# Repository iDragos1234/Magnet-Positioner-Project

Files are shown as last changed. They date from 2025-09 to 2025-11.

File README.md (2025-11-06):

# Magnet Positioner

## Introduction

Repository for the course _QIST4500 Multidisciplinary Team Project_.
In this course, our team had the task of building a gantry system used in positioning an external permanent magnet, adapted to a certain model of dilution refrigerator.
This magnet is intended for quantum control of qubits inside the refrigerator, potentially achieving this without the superconducting coil inside the refrigerator giving a static uniaxial magnetic field $B_z$ [1].
The advantage of this method is that it saves more space inside the refrigerator, allowing for more electronics and wiring to be fitted inside the refrigerator [1]. 
Another advantage is that the direction of the magnetic field $B_z$ can be changed [1]. 
In hybrid operating mode (i.e., using both the external and the internal magnet), it was experimentally shown that this could result in increased coherence times over the internal-magnet-only operating mode, while single-qubit gate fidelities stay below the fault-tolerant threshold for quantum error correction [1].

## Contents

* `magnet_positioner_cad_design/`: Folder containing all CAD files for the magnet positioning system, including a STEP file of the whole assembly.

* `magnet_xyz_positioner_code/`: Code used to control the motors. Largely unchanged from the initial code given to us.

* `magnet_data/`: Magnet measurement used for motor calibration and mapping the magnetic field. At the moment, only measurements along the x-axis are included, on a 1D grid with 1 cm spacing between neighbouring points.

* `documents/`: Relevant documents for this project, including the final report and final presentation for this project.

* `magnet_simulation.ipynb/`: Magnetic field simulations with Magpylib of the magnet used in our project.

*  `plot_magnet_data.py`: Plot of the measurements in `magnet_data/`.

## References

[1] Yu, Cecile X., et al. "Optimising germanium hole spin qubits with a room-temperature magnet." arXiv preprint arXiv:2507.03390 (2025).

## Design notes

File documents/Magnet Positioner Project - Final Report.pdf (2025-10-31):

# Magnet Positioner

Dragos, Ileana, Nian Tian Lin, Qu Tianchen and Badr Zouggari

October 31, 2025

Abstract
With the continuous scaling of semiconductor qubit architecture, the need for more space within the dilution refrigerator becomes critical, as required by the ever increasing amount of wiring and electronics inside. In this context, the superconducting magnet inside the refrigerator can become a major bottleneck, occupying valuable space inside the dilution refrigerator. Here, we present the design and development of a permanent magnet positioner outside of the the fridge to fully replace the superconducting solenoid currently being used by the Veldhorst group at QuTech. The system was modelled and manufactured considering several success criteria. To study the effect of the magnetic field at the device location, we performed simulations of the field strength around the magnet and compared them with field measurements in a single direction. Although the assembly was not completed on time, this design still shows a promising approach at addressing future scalability concerns.

## 1 Introduction

### 1.1 Theory

Semiconductor spin qubits represent one of the early studied types of qubits, providing a natural two-level system, wherein a qubit is encoded in the state of a single spin 1/2 electron/hole confined in a semiconductor quantum dot [1], [2]. The small, nanometric size (∼ 100 nm) of quantum dots provides the benefit of dense integration of many qubits on a small quantum device [2], [3]. This is an important requirement for the realization of large-scale, fault-tolerant quantum computing, as well as for relevant applications in cryptography, all of which necessitate a large number of physical qubits (more than 10⁶
) [4], [5]. Additionally, manufacturing and scaling of semiconductor devices for spin qubits is facilitated by their similarity and compatibility with classical semiconductor devices (i.e., transistors) [3], [6]. One downside is that the complexity of circuitry needed to address qubits in such quantum processors increases fast with larger number of qubits, thus limiting the maximum number of quantum dots on such devices [2], [3].

Gallium-Arsenide (GaAs) for electron spin qubit devices emerged as a first promising platform for the realization of spin qubits. GaAs provided a sparse 2D electron gas (2DEG) and allowed to isolate few (or single) electrons into a 0D space. More recently, Germanium (Ge) hole spin qubit devices have also been employed, thanks to suppressed noise from hyperfine interactions when compared to GaAs, resulting in longer coherence times [6]. The limited hyperfine interactions in Ge stem from the low abundance of nonzero nuclear spins in the environment (with the possibility of further isotopic enrichment), but also from the p-type character of the valence band [6].

An important characteristic of Ge qubits is the strong natural spin-orbit coupling which acts as a double-edged sword. On one hand, it enables all-electrical control of qubits and fast gates through electron-dipole spin resonance (EDSR). This way, shorter gate times are achieved when compared to coherence times [7]. Moreover, no other microstructures (e.g., nanomagnets) are used to control the spin, as in the case of electron spin qubits [6].

On the other hand, strong spin-charge coupling and dependence of g factors on the applied electric field imply that charge noise becomes a major nuisance for hole-spin coherence [6]. Nevertheless, it is still possible to find “sweet spots” in qubit operation such that hole-spins are not affected by charge noise. The g-tensor features strong anisotropy, meaning that the out-of-plane and in-plane components (g⊥ and g∥, respectively) differ greatly (|g⊥| ≫ |g∥|) [6]. As most Ge devices require a strong magnetic field B, even small deviations of B from the g-tensor plane can greatly affect qubit properties, resulting in different quantization axes of qubits [8].

Furthermore, the hyperfine couplings become negligible when B is in-plane, due to the Ising characteristic of hyperfine interactions [8]. Hence, limiting hyperfine interactions requires finding a second “sweet-spot” in B field alignment, but this time with respect to the hyperfine plane.

Finding an optima such that B is aligned to both of the g-tensor and hyperfine interactions¹ planes can be hard and sensitive to small angle variations of B [6], [8], and might necessitate striking a balance between the two. In this context, changing the orientation of B appears as the natural solution.

### 1.2 Problem context

The Veldhorst research group at QuTech currently operates Ge hole-spin qubit experiments by using a superconducting solenoid to generate the uniaxial magnetic field B necessary for qubit control [9]. Specifically, the solenoid is a 3-0-0 Tesla (T) magnet, meaning it can create up to 3 T on a single axis, with a bore of 200 mm (∼ 190 mm sample space) supplied by Bluefors. The uniaxial nature of B prompted the group to install an additional gantry system for moving a permanent magnet outside the dilution refrigerator [9]. This permanent magnet is used to fine-tune the magnetic field at the qubit location, thereby solving one of the limitations of the solenoid. The experiment utilized a Ge/SiGe heterostucture processor, with 10 qubits arranged in a 2D array [7]; see figure 1. Superconducting vector magnets were proposed as an alternative solution[10], but were deemed unfeasible due to higher space and heat load considerations [9].

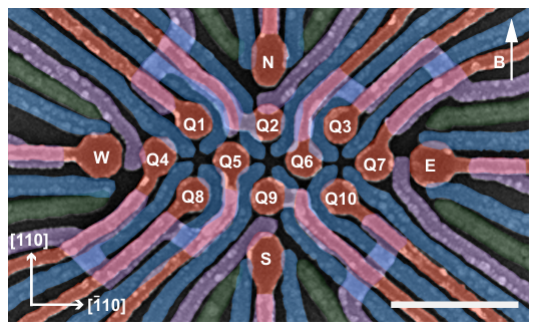
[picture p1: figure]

Figure 1: The 10 qubit physical processor (left) and its qubit layout used to test the external magnet positioner [7], [9].

While this configuration functions effectively for small-scale demonstrations with approximately 10 qubits, it presents an obstacle for the planned transition to the 1000 quantum dot project, where every bit of space inside the fridge is valuable. A successful demonstration of qubit control with the superconducting solenoid turned off and only using the permanent magnet underscores the possibility to remove the solenoid entirely [9].

A successful resolution of this challenge can have a positive impact on the scalability of semiconductor spin qubits. The dilution refrigerator’s interior represents a fixed, finite resource. However, superconducting magnets, while providing excellent field control, consume critical volume that could otherwise house cryogenic control electronics, signal conditioning components, and extensive wiring necessary for operating hundreds or thousands of qubits. Recent demonstrations have shown that room-temperature permanent magnets positioned external to the cryostat can achieve comparable qubit performance metrics, including dephasing times T

∗
2 = 13 µs and gate fidelities exceeding 99.9% [9]. This breakthrough suggests that relocating the magnetic field source outside the refrigerator is technically feasible and could unlock the spatial capacity required for qubit scale-up.

## 2 Problem statement, scope, and success criteria

### 2.1 The Core Challenge: space limitations in scaled qubit systems

Each qubit in semiconductor quantum processors uses dedicated wiring for control and readout operations. As the qubit count increases proportionally, so does the demand for coaxial lines, DC

1
It is worth noting that isotopic enrichment can remove hyperfine couplings and thus simplify this problem, to the extent that the optima for the g-tensor in-plane alignment of B dominates [8].

connections, and cryogenic electronics housed within the dilution refrigerator. The superconducting solenoid currently occupies valuable space inside the cryostat, space that must be reclaimed to accommodate the extensive circuitry required for 1000 quantum dots. Without addressing this constraint, the integration of necessary control infrastructure becomes physically impossible, effectively halting scalability efforts.

Therefore, the problem statement can be summarized as follows:

To enable scaling quantum processors from tens to thousands of qubits, an improved magnet positioning system must be designed to replace the bulky superconducting solenoid inside the dilution refrigerator, reclaiming essential space for expanded wiring and electronics.

### 2.2 Magnetic field alignment requirements

Germanium hole spin qubits exhibit strong spin-orbit interaction, which enables high-fidelity quantum gates but simultaneously creates a pronounced dependence on magnetic field orientation [9]. Precise alignment of the magnetic field to the sample plane is essential to minimize dephasing from hyperfine interactions and maximize spin control fidelity [9]. Current experiments using superconducting solenoid magnets achieve single-qubit Clifford gate fidelities above 99.9% [9]. Any alternative magnetic field solution must maintain this level of precision while simultaneously addressing the space constraints.

### 2.3 Scope of the project

In this section, the initial scope of the project is discussed. This scope was established following discussions between the team had and the project supervisor, wherein different technical challenges and initial solutions were pointed out, as outlined below. This project focuses on adapting an existing prototype magnet positioner system to the ProteoxMX dilution refrigerator in QuTech’s laboratory.

### 2.3.1 Technical challenges

- Adapting New Fridge Layout: Previously, the magnet positioner was designed for a smaller Bluefors cryogenic fridge with a different layout. In order to utilize a magnet positioner for the new ProteoxMX fridge, a new adapted frame is needed. At the same time, aiming for component reusability across the two design is desired.
- Cryogenic Temperature Effects: The Meissner effect in superconducting materials within the refrigerator can distort magnetic field distributions at different temperature stages. Understanding these temperature-dependent field modifications could be very helpful for maintaining consistent qubit operation.
- Mechanical Vibration Control: Eddy currents induced in conductive materials by moving permanent magnets can generate vibrations that propagate through the refrigerator structure. These vibrations translate to magnetic field fluctuations at the qubit location, directly degrading coherence times [11]. The project could incorporate some sort of damping mechanism to attenuate vibrations and improve overall system stability.
- Precision Positioning: Achieving 0.1 mm positioning accuracy requires careful attention to motor selection, control algorithms, and mechanical transmission systems. The implementation will explore servo-motor upgrades and gear systems between motors and leadscrews to enhance positioning precision.
- Safety Considerations: Strong permanent magnets present hazards during operation and failure scenarios. The design should include physical stops to catch the carriage in case of mechanical failure and non-magnetic rails for z-axis movement to prevent unwanted magnetic interactions.

Certain aspects lie beyond the current project scope. The design and fabrication of the qubit samples themselves, while connected to the magnet system performance, remain separate efforts. Additionally, the project focuses on the ProteoxMX [12] system; while insights may inform future adaptations to other refrigerator models, explicit multi-system compatibility is not a primary objective.

### 2.4 Success Criteria

### 2.4.1 Quantitative performance targets

- Positioning Precision: Motor control systems must achieve positioning accuracy of at least 0.1 mm in all three axes (X, Y, Z). This tolerance ensures that magnetic field variations due to positional uncertainty remain negligible compared to the qubit’s field sensitivity.
- Magnetic Field Range and Control: The system must generate magnetic fields continuously adjustable up to 25 mT at the sample location.
- Qubit Performance Preservation: The adapted magnet positioner must enable qubit dephasing times T

∗
2 at least equal to current performance with the superconducting solenoid.
- Gate Fidelity Maintenance: Single-qubit gate fidelities of ≥ 99.9% must be achieved in benchmarking tests using the external magnet system.

### 2.4.2 Functional requirements

- Magnetic Field Mapping Capability: The system must enable comprehensive characterization of the magnetic field distribution around the sample location.
- Structural Stability: The mechanical structure must exhibit sufficient rigidity to minimize vibration-induced magnetic field fluctuations.

### 2.5 Approach and implementation strategy

The project leverages a proven concept—the gantry-style permanent magnet positioner demonstrated in recent germanium qubit experiments [9]. This approach positions a room-temperature permanent magnet on a three-axis positioning system located beneath the dilution refrigerator. By maintaining the magnet external to the cryostat, the entire volume previously occupied by the superconducting solenoid becomes available for qubit sample infrastructure [9].

### 2.5.1 Advantages of the external permanent magnet approach

- Eliminates the need for bulky superconducting coils and associated infrastructure inside the cryostat, freeing space for qubit wiring and electronics [9].
- Permanent magnets require no electrical power during operation, removing a heat load source from the cryogenic environment [11].
- Comparable or superior qubit coherence times relative to superconducting solenoids, possibly due to reduced magnetic field noise [11].
- Allows in-situ adjustment of field strength and orientation without warming the refrigerator or disrupting experiments [9].

### 2.5.2 Trade-offs and limitations

- Permanent magnets generate fixed intrinsic field strengths, making continuous field adjustment more complex [9].
- Positioning mechanism introduces moving parts, creating potential vibration sources that require active damping.
- Strong permanent magnets necessitate proper shielding, mechanical stops, and careful handling.

Alternative approaches considered include hybrid systems and Halbach arrays, but the gantry-style positioning system offers the most direct path to reclaiming cryostat space while maintaining the required field control for high-fidelity qubit operations [9].

## 3 Methods and approaches

The following section will include the various steps and approaches taken to produce the magnet positioner assembly as shown in Fig. 2. The assembly is largely based on the design created by Yu et al. [9], which are improved upon to accommodate for a larger fridge and stronger magnet. The assembly was made using Autodesk Inventor, a CAD software used for 3D mechanical design and simulation. The system can be separated into a stationary part called the gantry frame and a movable part categorized as the xyz-assembly.

### 3.1 xyz movement

The movement of the magnet makes use of four NEMA 17 stepper motors with a maximum holding torque of 0.55 Nm. This choice is inspired by the way 3D printers and CNC machines operate, which enables motion on the three axes of the Cartesian coordinate system.

Using a lead screw with a 8 mm diameter and 2 mm pitch, this translates into a maximum load of ∼ 36 kg per motor, where we show the calculation in Appendix A. However, to account for the fact that the moving torque will be less than the holding torque and to allow for a margin of error, each motor should not exceed 50% of the maximum load (i.e. 18 kg per motor).

The motors are controlled with a CNC shield V3 connected to an arduino UNO board. This enables movement of three motors for all three axes with a fourth motor that can be synchronized on any axis. In this case, two motors are used to move the z direction and the remaining two move the x and y directions respectively.

To improve the positioning precision mentioned in Section 2.4.1, we have replaced the original lead screw trapezoidal nuts in the x and y directions with spring loaded anti-backlash nuts. This adds tension on the screw from both directions and prevents any unwanted motion caused by loose fitting between the two parts. A similar replacement in the z direction is not necessary, since gravity acts as a ‘natural’ anti-backlash mechanism already.

We include several SBR16 linear rails to support and guide the movement of the motors along the y and z directions. An MGN12H slider is used for the x direction.

### 3.2 Material choices

An important step in the design is to select the best materials for each part, which are influenced by several factors listed below:

- Weight: The xyz assembly in particular requires special attention due to the motors having a weight limitation as shown in Section 3.1.
- Magnetic properties: Since we work with a strong magnet, it is important to consider non-magnetic materials for safety but also to not influence the magnetic field created by the magnet.
- Rigidity: Depending on the functionality of the component, rigidity might have a higher or lower priority. Critical parts that are important for structural support require high rigidity to be able to hold up the frames above. In contrast, a stepper motor bracket can have low rigidity.

Considering the above factors, our choice of materials narrows down to three different kinds: stainless steel, PLA² filament and aluminium alloy.

While stainless steel has a high density, it offers high rigidity in return. This makes it a good option for small components that are important for stability of the entire system. For example, the z plate brackets are crucial components to connect the xyz assembly with the gantry frame. These parts are small, but have to support a lot of weight.

PLA is very lightweight with low durability and parts made from it can be easily done by a 3D printer. Any parts that hold something small in place and are not needed for the structure of the

2PLA is polylactic acid, the plastic filament used for 3D printing.

system, will be created from this material.

Aluminium alloy has a roughly three times lower density compared to stainless steel while still offering good rigidity, although not as high as stainless steel. Therefore, any large piece that will heavily impact the total weight of the assembly can be made from aluminium alloy.

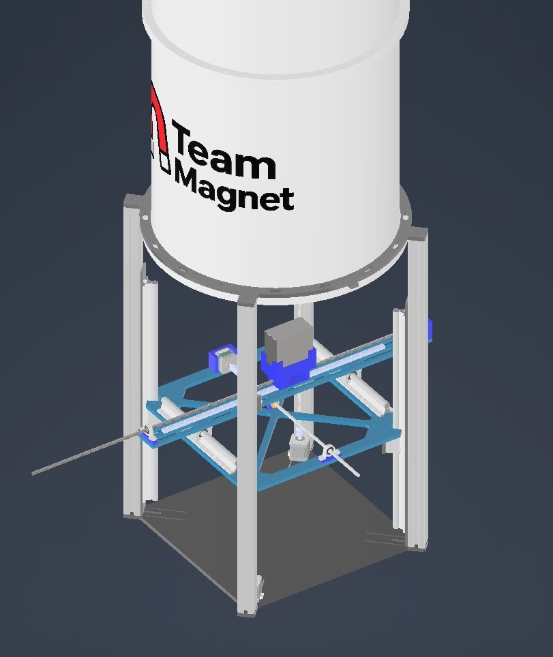
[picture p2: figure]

Figure 2: Full magnet positioner assembly attached to a cylindrical dilution refrigerator.

### 3.3 Gantry frame

Fig. 3 shows the gantry frame, which is the static outer frame of the system. The half rings and base plate are made from aluminium alloy while any brackets for vertical movement are created using stainless steel.

At the top, a ring shape is used to fit with and rest onto the rim of the dilution fridge. Compared to the smaller fridge from Ref. [9], the ProteoxMX fridge has 8 equidistant bolts protruding from the rim with 3 additional bolts appearing irregularly on halfway points between some of the regularly spaced bolts. To account for the 11 extra bolts, we have decided to create 16 holes spaced evenly (at every 22.5 degrees) around the ring. This allows for some amount of freedom to place the magnet positioner in the desired orientation. Notably, the holes themselves are designed large enough to enable up to 4 degrees of movement.

The base plate on the bottom, aside from the increased size, remains largely the same. A small modification is the addition of slotted holes in the corners of the base plate. This allows the base plate to be compatible with multiple fridge sizes, potentially future-proofing this design.

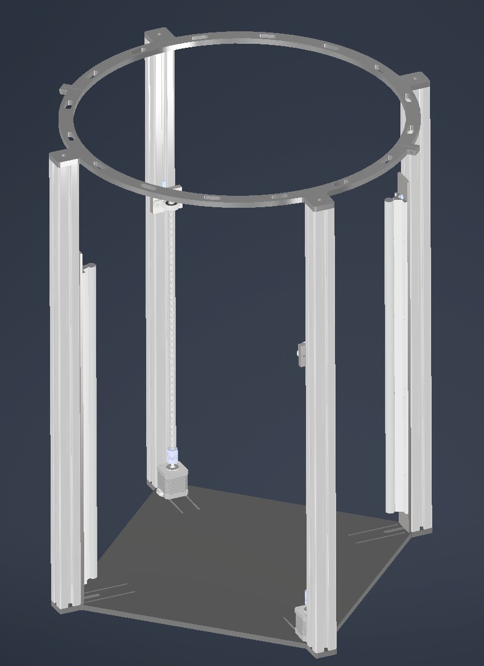
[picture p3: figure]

Figure 3: Gantry frame of the magnet positioner. The main components consist of three parts. Two half rings are created to rest on the bottom rim of the fridge, the z translation parts enable vertical movement and the base plate connects the four pillars to create a stable base.

### 3.4 xyz-assembly

Fig. 4 shows the assembly that is able to move on the z axis using the motors and rails connected to the gantry frame. Fig. 5 is mounted on top and can be moved in the y direction. Finally, the magnet itself can be moved on the guide rail in the x direction.

All of the parts indicated with dark blue and purple are not integral to the structural stability and are therefore 3D printed. The pillow block bearings and motors are mounted on top of brackets to make sure they are aligned with each other.

The plates indicated with light blue are made from aluminium alloy. The triangle shaped cutouts in Fig. 4 are added to reduce the weight of the plate without strongly impacting the structural integrity of the component. Similarly, the plate in Fig. 5 rectangular cutouts.

Before starting the manufacturing procedure of the parts, we inferred the entire weight of the xyz assembly from the CAD files. This showed that the xyz assembly totaled around 13 kg, staying well within the margin that two motors can handle in the z direction.

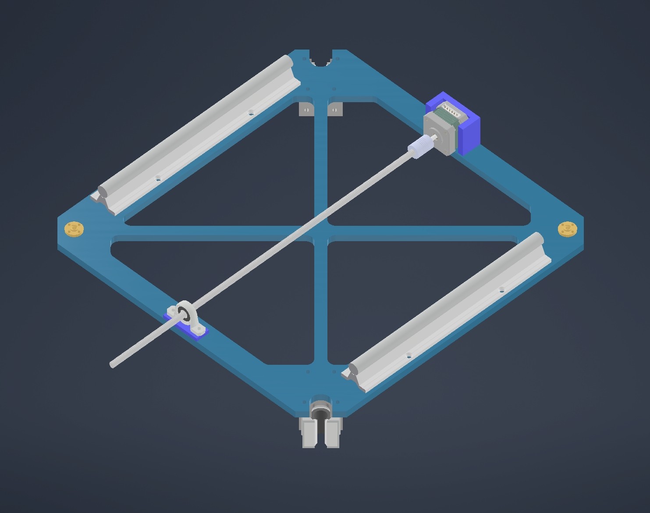
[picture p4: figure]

Figure 4: Diagram showing the movable frame of the magnet positioner in the z direction

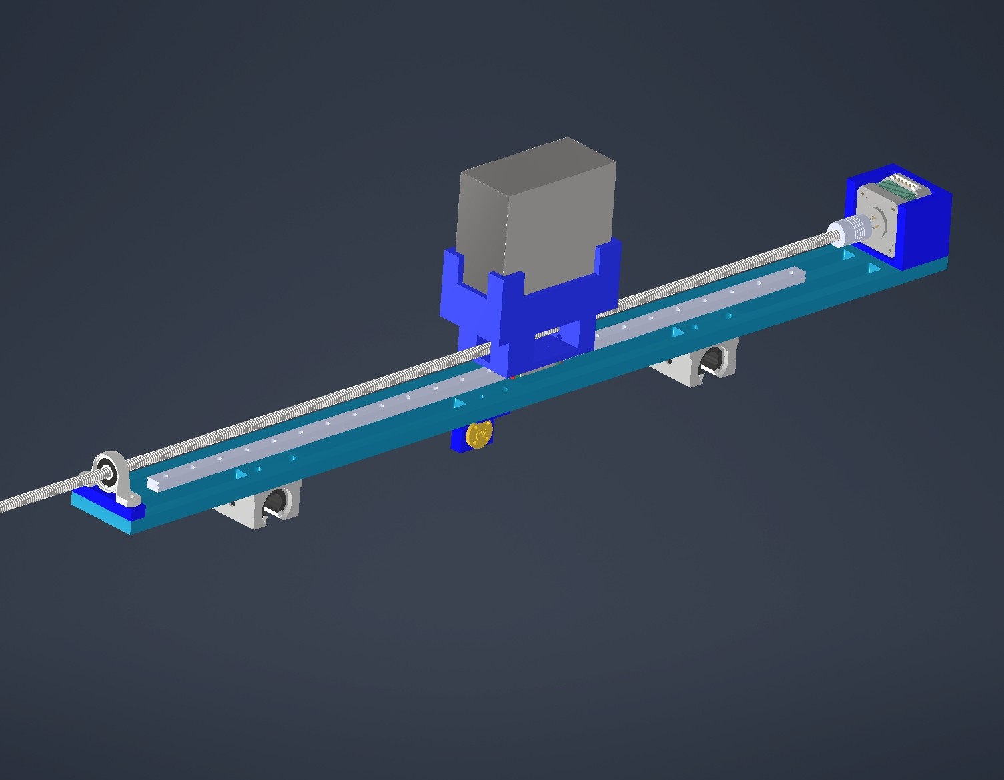
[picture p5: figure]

Figure 5: Diagram showing the movable frame of the magnet positioner in the y direction. Additionally, the magnet holder itself is movable in the x direction

## 4 Results

Our results pertain mostly to measurements of the magnetic field as its x-axis position is varied. Due to an unexpected delay in the plate fabrication, we were not able to assemble the whole magnet positioner by the time this report is written. However, we are able to theoretically analyse the magnet performance and, with the help of simulation, verify the viability of the approach.

### 4.1 Magnetic field at different distances

We measure the field strength with a 3D Hall sensor³
. The measurement setup can be seen in Fig. 6 where we move the sensor perpendicular from the centre of the magnet. We log the measurement data using evaluation software developed by Infineon Technologies that is compatible with the Hall sensor. The resulting mean field strength can be seen in Fig. 8. Here, we also compare it to the simulation using Magpylib [13][14]. This helps us verify the correctness of our simulation. The simulation is normalized by setting the magnetic field strength to be equal to the measurement result for a distance of 7cm.
The simulation of overall magnetic field in the x-y plane can be seen in Fig. 7.

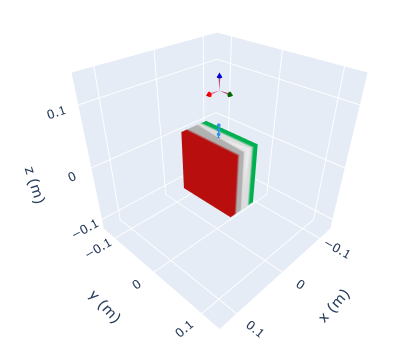
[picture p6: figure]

Figure 6: The sensor is at the centre of the magnet. Here, we move the magnet instead of the sensor. This specific instance has a 7cm distance. The red and green colour on the magnet shows its magnetisation direction and the coordinate arrows show the sensor location. The blue dotted line shows the movement for adjusting distance.

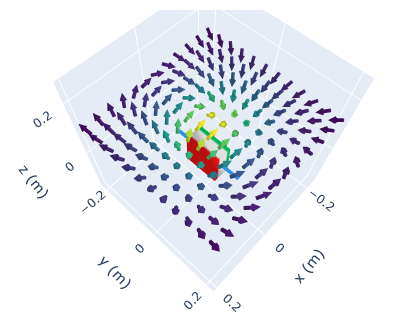
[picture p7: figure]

Figure 7: Since the magnetic field reaches the target 25mT in practice when 7cm away from the magnet surface, we show here the field distribution with z=7cm

3Model TLE493DW2B6MS2GOTOBO1 from Infineon Technologies

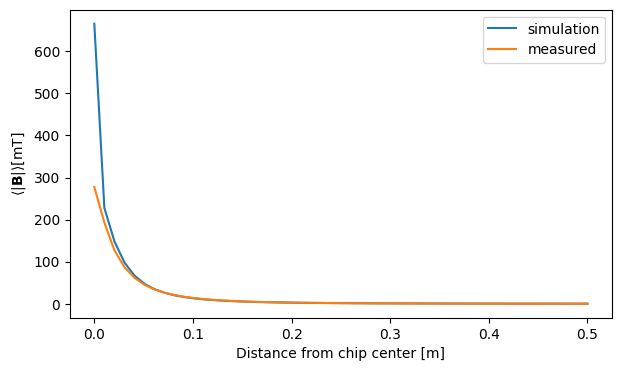
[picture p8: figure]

Figure 8: The mean field amplitude when chip is at different distances from the magnet.

### 4.2 Inhomogeneity of the magnetic field

The size of a quantum dot is at nanometer scale; therefore, although the magnetic field provided by the external permanent magnet is far from uniform, a chip with few quantum dots still experiences a close to uniform field. However, this could be a concern as one scales up the number of quantum dots on a single chip. In the Veldhorst lab, people are interested in making a 1000 quantum dot chip, with a 10∗100 square layout, where the distance between each adjacent dot is 200nm, making the quantum dots take a 20µm∗2µm area. For simplicity, we assume the chip to be a 20µm∗20µm square. This raises the question how much influence the inhomogeneity of the magnetic field will have on the future 1000 quantum dot chip.
To address this, we introduce a new quantity called deviation. For all possible magnetic field values on the chip {Bi}, the deviation d is

d = max
r,r

′
in chip

||B(r) − B(r

′
)||2

||Bchip||2

. | (1)

Which represents the maximum vector difference relative to the mean amplitude of the field across the chip.
This deviation can be estimated theoretically with the dipole moment approximation. Assuming that the magnet has a dipole moment m we can recall that the magnetic field can be approximated as:
B(r) = µ0
4π
3r(m · r)
r

5

−

m
r

3

(2)

We switch to the spherical coordinate where magnetic moment m is pointing at the positive direction of the z-axis
B(r, θ, ϕ) = µ0
4π
3|m| cos θ
r

3

rˆ −

m
r

3

(3)
Since we are already using dipole approximation, we are only interested in the first order effect of the field, which is captured by the gradient ∇B:

∂B
∂r =

−3µ0
4π
3|m| cos θ
r

4

rˆ −

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
∂θ = −

µ0
4π

3|m|sin θ
r

3

rˆ | (6)

∂B
∂ϕ = 0 | (7)

The deviation can be first-order approximated as

d = max
a∈{0}×[0,a]×[0,a]

||a · ∇B||2
||B||2

(8)

where a is some relative position within the chip with width a.
Since we want in-plane magnetic field, the chip position will be perpendicular to the moment m · r = 0 or θ =

π
2

and thus the first term in dipole magnetic field expression vanish, thus

∂B

∂θ m·r=0

= −3||B||2r. ˆ | (9)

Thus if we express the gradient in normalized ˆr, ˆθ, ϕˆ basis

∇B
||B||2
θ= π
2

=

3
r

ˆθ −
3
r

rˆ 0

(10)

We see that the deviation will have the same 3
r

decay in the ˆr or ˆθ direction, but it will vanish in the ϕˆ direction. Since our chip is in ˆθ − ϕˆ plane, the deviation is

d =

3a
r

(11)

Deviation with other chip orientations can also be derived from (10).
In order to cross-check whether the dipole approximation fits our case, we also perform a simulation. Here, we assume that permeability is constant and the magnet has uniform magnetisation. To evaluate the magnetic field gradient, we use the same setup as the previous subsection as seen in Fig. 6.
We collect samples {Bi} of the magnetic field from 400 evenly spaced locations in the 20µm × 20µm chip and the deviation estimator becomes:

d = max
i,j

||Bi − Bj ||2
⟨||B||2⟩

Note that deviation as a relative quantity is independent of the magnetisation strength of the actual magnet.

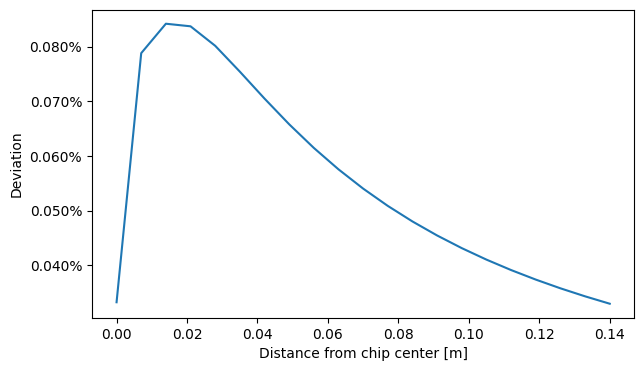
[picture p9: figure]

Figure 9: The deviation when chip is at different distances from the magnet.

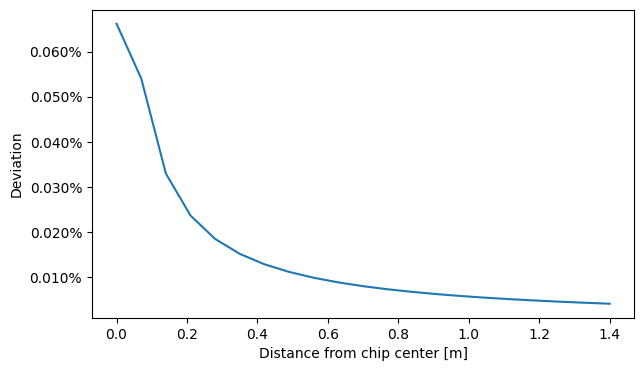
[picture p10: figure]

Figure 10: We see full dipole approximation regime for z > 0.2m.

From the simulation results in Fig. 9,10, we can see that the magnetic deviation is more than three orders of magnitude lower than the mean magnetic field. Since in fabrication it is common to have the g-factor vary by a factor of 2 across different quantum dots [15], the magnetic field gradient will not be the dominating term for qubit frequency fluctuations.

We also see that deviation decreases as expected from our theoretical report except when the distance is very close. This is expected since the dipole approximation breaks down in close range. Instead, we see a sharp increase from zero. Low deviation for a close chip is largely due to the magnetic field being almost uniform near its surface. Thus we have a peak deviation between uniform approximation regime and dipolar approximation regime.

We may also be interested in how the deviation depends, on the orientation of the chip. We choose the distance to be 7cm where the field is around 25mT. Here, we also see how the simulation fits accurately with the theoretical prediction.

When rotating along the ˆθ direction in Fig. 11, we see two peak deviations at π/2 and 3π/2. with peak value being √
2 times higher than the minimum value. Since the chip is in ˆr − ˆθ plane, the deviation has contribution from both directions

d = ||³a
r

ˆθ −

3a
r

rˆ||2 =

3

√
2a
r

(12)

When rotating along the ϕˆ direction in Fig. 12, since contributions are the same from ˆr and ˆθ, we see no deviation difference up to first order.
When rotating along the ˆr direction in Fig. 13, the chip remain in ˆθ−ϕˆ plane. However rotating the square chip changes the maximum distance of the ˆθ direction as it vary from side length to diagonal length. Thus we see 4 peaks at π/4, 3π/4, 5π/4, 7π/4 with the peak √
2 times bigger than
the minimum deviation.
Therefore, different orientations of the chip will result in at most a factor of √ 2 difference for
the deviation.

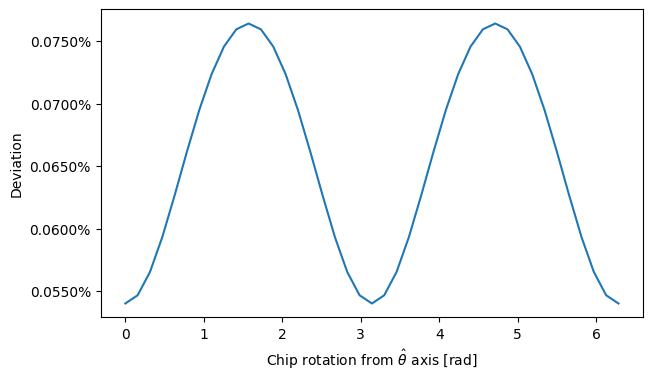
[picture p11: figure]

Figure 11: The deviation when chip is at different distances from the magnet.

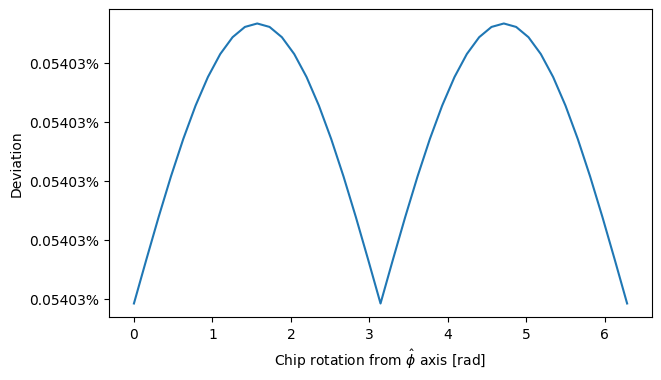
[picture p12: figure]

Figure 12: The deviation when chip is at different distances from the magnet.

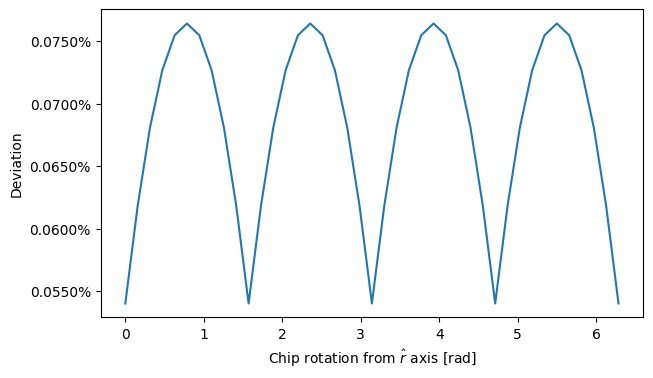
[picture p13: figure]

Figure 13: The deviation when chip is at different distances from the magnet.

### 4.3 Noise analysis

The next thing we want to estimate is the potential noise an external magnet can bring to the qubit. In previous work [9], the hysteresis effect is observed from the motor for magnet movement. This leads to approximately 50µm offset per start-and stop event for the movement of 1mm. However, this should not be considered as decohering noise since such an offset can be predicted/compensated. Also, such an offset only exists when we want to reposition the magnet and can be accurately measured when the magnet is still. The main noise comes from potential random vibration of the positioner, which is more prone to these disturbances since the magnet is no longer inside the concealed fridge.

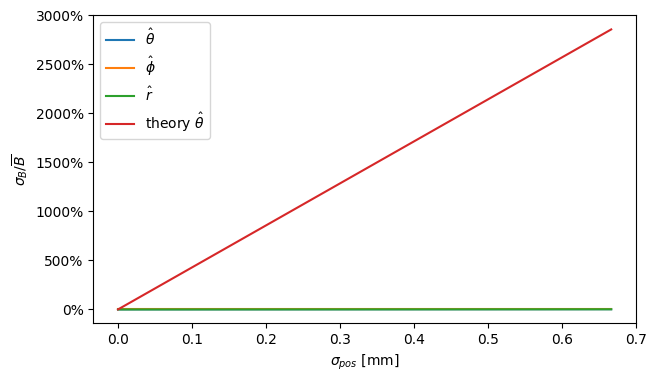
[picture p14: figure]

Figure 14: The deviation when chip is at different distances from the magnet. We also show the theoretical prediction of the dependency for ˆθ direction, which is in line with simulation result.

The Larmor frequency of quantum dot qubits usually ranges from a few hundred MHz to a few GHz. In comparison, the mechanical vibration of the positioner has a far lower frequency. Thus, we can model noise from the magnet as a quasistatic noise. Assuming that the offset amplitude of

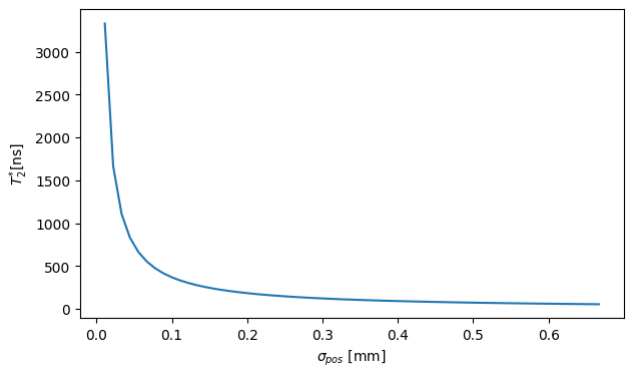
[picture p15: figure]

Figure 15: How T

∗
2 depend on the standard deviation of the magnet position.

the magnet follows a gaussian distribution that does not exceed 2mm, aka 3σpos < 2mm. Since the fluctuations are small, the resulting magnetic deviation also follows a gaussian distribution, and the relation can be calculated using (10) in the same way we calculated the deviation in the previous section. From Fig. 14, we see that only vibration from the ˆr, ˆθ direction will cause magnetic field fluctuation. At the same time, only ˆr direction vibration will have a magnetic field deviation in ˆθ direction – parallel to the magnetic field, which has a first order effect on the magnetic field amplitude. Since the larmor frequency is proportional to the field amplitude, the resulting Larmor frequency distribution becomes

P(ω) = 1
√
2πσω

e

−

(ω−ωL)

2

2σ2
| ω | (13)

σω = ωL

σB
B
= ωL | 3σpos,r
r
| | (14)

For quasistatic noise, the coherence function is the Fourier transform of the noise distribution from which we can deduce T

∗
2

time:

f(t) = ⟨S

+(t)⟩ = ⟨S

+

Z +∞

−∞

P(ω)e

itωdω⟩ | (15)

= ⟨S

+e

iωLt
e

−σ2
ωt

2
2 | ⟩ | (16)

= f(0)e

iωLt
e

−σ2
ωt

2
2 | | (17)

= f(0)e

iωLt
e

− ¹
2
| t T ∗
| 2

2
, T ∗
2 =

1
σω
| | (18)

We will thus have a gaussian decay for the qubit coherence with relaxation time T

∗
2
| | inverse
to σω. From Fig. 15, we can see the estimation of T

∗
2

time assuming the larmor frequency to be 1GHz. We can see that for strong vibration, the T

∗
2

is considerably affected. Although we can argue that such quasistatic noise can be largely cancelled by dynamical decoupling, we still see that such a positioner could be sensitive to mechanical vibration in certain cases.

In conclusion, the T

∗
2

is sensitive to vibration on the ˆr direction and could affect the qubit performance when strong vibration exists. Given the setup in our positioner, this corresponds to vertical vibration of the magnet.

### 4.4 Data management

All CAD designs for the complete setup, along with the specific parts discussed in Chapter 3, and the simulation data outlined in this chapter with the associated code, are available in our GitHub repository [16].

## 5 Discussion

### 5.1 Reflection

The development of the magnet positioning system was not fully completed due to delays in the delivery of several critical manufactured components. These parts, mainly the X-plate and Z-plate which were essential for the mechanical assembly and calibration of the positioning mechanism, did not arrive in time to allow for integration and testing during the project period. As a result, key functionalities such as positional feedback verification and dynamic control tuning could not be carried out as planned.

The delay was mainly due to our reliance on external manufacturing and the lack of sufficient buffer time in the project schedule to account for possible production or shipping setbacks. Additionally, some design iterations were finalized later than expected, which further compressed the available window for ordering and assembly.

In retrospect, this issue could have been mitigated through earlier procurement planning and risk management. Placing the manufacturing orders sooner, or designing provisional substitute components for early-stage testing could have reduced dependency on external timelines. Improved communication with the manufacturer to track progress and confirm lead times would also have helped anticipate and respond to potential delays.

### 5.2 Success criteria evaluation

Even though we were not able to finalize the product, we were still able to achieve some intermediate progress. This progress will be assessed by evaluating our success criteria.
The project began with a set of predefined success criteria that guided the design and development of the magnet positioning system. In this section, we reflect on how these criteria were addressed and evaluate the corresponding outcomes.
- Positioning Precision: The motor control system was required to achieve a positioning accuracy of at least 0.1 mm in all three spatial axes to ensure magnetic field stability relative to the qubit’s field sensitivity. Due to the incomplete assembly of the mechanical structure, this specification could only be experimentally verified in the x direction with the anti backlash nut. However, the same principle should apply for the y direction.
- Magnetic Field Range and Control: The system was designed to provide continuously adjustable magnetic fields up to 25 mT at the sample location. Based on measurements compared to simulation results and magnetic field calculations (described in section 4.1), we are confident that the current electromagnet configuration fulfills this requirement. The range of the magnet positioner in the Z-direction was designed with these specific requirements in mind.
- Qubit Performance Preservation: A key criterion was ensuring that the new magnet positioner maintains qubit dephasing times (T

∗
2

) comparable to those obtained using the existing superconducting solenoid. Since the physical assembly was not completed, this verification could not be performed. This assessment will ultimately depend on future testing conducted by the research group that integrates the system with their qubit setup. Instead, we estimated the T

∗
2

for the qubit with reasonable assumptions and simulation. It shows the T

∗
2

is sensitive to the vibration strength and it is only sensitive to vibrations perpendicular to the magnet. In our framework, this correspond to vertical vibration.

- Gate Fidelity Maintenance: Achieving single-qubit gate fidelities of at least 99.9% in benchmarking tests requires integration of the magnet system with the quantum hardware. As testing was contingent upon a completed setup, this requirement remains to be verified in collaboration with the end users during the next stage of project deployment.

- Magnetic Field Mapping Capability: Making use of a Hall sensor with associated evaluation software, we showed the capability to log and save the magnetic field measurements in a single direction. Furthermore, after some postprocessing we were able to visualize the field strength and compare it to our simulations which can be seen in Fig. 6. Hence, we believe that the full mapping of the magnetic field is also possible once the entire assembly is completed.
- Structural Stability: The structural design aims to minimize vibration-induced field fluctuations through high rigidity and reduced mechanical resonance. Although the final structure has not yet been assembled, material choices and design simulations indicate that the mechanical stability criterion is likely to be met once manufacturing and integration are completed.

In summary, the success criteria related to positioning precision, magnetic field range and mapping capability were partially achieved within the scope of the project. Criteria dependent on the physical assembly and integration, such as positioning precision, qubit performance preservation, gate fidelity maintenance, and structural stability, remain to be validated. Overall, the design phase established a strong foundation to meet all goals once the remaining components are delivered and assembled.

### 5.3 Future Plan of Attack

This section outlines a proposed plan for achieving and validating the success criteria that were not fully met during the initial project phase. Each subsection focuses on a specific criterium, detailing methods of assessment, potential challenges, and further steps to ensure successful realization.

### 5.3.1 Positioning Precision

To verify the required positioning accuracy of better than 0.1 mm in all three axes, precision calibration experiments will be conducted once the mechanical structure is assembled. The plan could include integrating high-resolution optical encoders or laser displacement sensors onto each axis to measure actual movement relative to commanded positions.

Evaluation will involve repeated motion sequences and comparison between commanded and measured displacements to determine both static and dynamic precision. If deviations exceed the tolerance, potential improvements include refining motor control parameters, improving the mounting rigidity, or looking into higher quality motors.

### 5.3.2 Qubit Performance Preservation

To assess the influence of the magnet positioner on qubit dephasing times (T

∗
2

), the system will be
tested in conjunction with a qubit setup operated by the partner research group. The procedure involves performing Ramsey or spin echo experiments under various magnetic field configurations generated by the positioner. The resulting T

∗
2 values will be compared to baseline results obtained with the superconducting solenoid.

Should the T

∗
2

times degrade noticeably, the next step will be to identify possible noise sources introduced by the new system, such as current fluctuations, magnetic field instabilities, or mechanical vibrations. Adjusting current stabilization, improving shielding, or refining control electronics could be considered to mitigate these effects.

### 5.3.3 Gate Fidelity Maintenance

The goal of maintaining gate fidelities above 99.9% can be tested using randomized benchmarking experiments with the magnet positioner integrated into the quantum hardware setup. This approach quantifies the average error per gate under varying magnetic field conditions.

If the measured fidelities fall below the target value, diagnostic tests should be performed to identify whether the issue stems from magnetic field noise, cross-talk between control channels, or thermal effects induced by the magnet coils. Based on these findings, the control algorithms and magnetic stabilization methods can be optimized, or additional passive and active noise suppression techniques can be introduced.

### 5.3.4 Structural Stability

After assembly, the structural stability will be experimentally validated by measuring vibration spectra of the positioning system during operation. This can be achieved using accelerometers or laser vibrometers attached to key structural components. The amplitude and frequency of mechanical oscillations will be compared to the frequencies relevant to qubit sensitivity.

If significant vibration modes are detected near critical operating frequencies, reinforcement of the frame or damping materials can be introduced to shift resonances away from sensitive bands. Additionally, mechanical coupling between moving parts can be optimized to further minimize unwanted vibrations.

## 6 Interdisciplinarity and teamwork

In this section, the various scientific disciplines explored in this project are discussed, as well as the teamwork during the project.

### 6.1 Interdisciplinary aspects

The interdisciplinary aspects of the Magnet Positioner project are central to both the process and the solution, drawing on expertise and methodologies from physics, engineering, computer science, and system design.

The project leverages methods and knowledge from quantum physics to define the requirements for magnetic field alignment and qubit performance, as well as to interpret simulation results relating to magnetic noise and field homogeneity. Engineering design principles guide the development of hardware structures, including the selection of materials for rigidity, weight, and magnetic properties, and the mechanical design of the gantry frame and xyz-movement assembly. Computer science and automation are incorporated through the use of CAD modeling (Autodesk Inventor) for 3D simulation, control algorithms for the stepper motors (Arduino UNO interface), and data analysis software for magnetic field mapping and real-time monitoring.

The process brings together simulation-based analysis, mechanical design, electronic control, and risk management strategies. The solution’s success criteria span quantitative (positioning accuracy, field range, gate fidelity) and qualitative (mechanical stability, safety protocols) metrics, requiring cross-disciplinary knowledge and skills.

### 6.2 Collaboration and team dynamics

At the start of the project, each member of the team already had some idea where there interests would lie within this project. As explained in the section above, the project consisted of various disciplines, where each member of the team felt slightly more comfortable to some disciplines than others. Given the various engineering aspects to this projects, each member of the team could start the project with a certain focus (e.g. figuring out the motors or starting with the CAD design). We would meet up often to show each other what we worked on, which made the start of the project very smooth. Moreover, all the team members were interested in all the aspects of the project, which meant that the team would have numerous useful discussions about what the next steps would be. This way of working persisted throughout the duration of the project and all team members are content with the way it went.

However, the project was not finished in time, which begs the question of how this came to be. The team suspects that this could have been avoided if the team was more conscious of the manufacturing times of the parts. Many critical parts are still not finished, which was the main reason this project could not be finished in time. Some delays were out of the control of the team, however this situation could have been avoided if the urgency had existed right at the start of the project. In hindsight, the team should have treated the manufacturing team with more urgency. Moreover, dummy parts could have been designed and manufactured to at least provide some clarity on some of the success criteria.

All in all, the team does feel that a lot has been accomplished during the duration of the project. This includes: a complete CAD design of the magnet positioner, motor testing with some of the bigger and heavier parts, magnetic field simulations and software to map the magnetic field with a comparison to real measurements, albeit only in one direction. Even though the project was not completed as we envisioned it to be at the start, the team is confident that a future project team can build upon our results and finish the project as it was intended to be.

## 7 Acknowledgments

During this project, we have had the absolute pleasure of working together with our team supervisor, Sasha Ivlev. He has been an enormous help during the process by answering our questions, providing new ideas and feedback, and providing guidance during the entire process. The team would like to thank him for the opportunity to work together on this project and hope that our work will be useful to him and the entire research group. Additionally, the team would like to thank the manufacturing team, specifically Nico Alberts, by providing us with guidance during the design process and the fabrication of tailor-made builds.

The team would also like to acknowledge that the usage of AI was limited during the entirety of the project, with some exceptions to help with literature review and understanding theoretical concepts better.

## References

[1] D. Loss and D. P. DiVincenzo, “Quantum computation with quantum dots,” Physical Review A, vol. 57, no. 1, pp. 120–126, Jan. 1998, issn: 1094-1622. doi: 10.1103/physreva.57.120. (https://doi.org/10.1103/physreva.57.120) [Online]. Available: http://dx.doi.org/10.1103/PhysRevA.57.120.
[2] G. Burkard, T. D. Ladd, A. Pan, J. M. Nichol, and J. R. Petta, “Semiconductor spin qubits,” Rev. Mod. Phys., vol. 95, p. 025 003, 2 Jun. 2023. doi: 10.1103/RevModPhys.95.025003. (https://doi.org/10.1103/RevModPhys.95.025003) [Online]. Available: https://link.aps.org/doi/10.1103/RevModPhys.95.025003.
[3] L. M. K. Vandersypen et al., “Interfacing spin qubits in quantum dots and donors—hot, dense, and coherent,” npj Quantum Information, vol. 3, no. 1, Sep. 2017, issn: 2056-6387. doi: 10.1038/s41534-017-0038-y. (https://doi.org/10.1038/s41534-017-0038-y) [Online]. Available: http://dx.doi.org/10.1038/s41534-017-0038-y. (http://dx.doi.org/10.1038/s41534-017-0038-y)
[4] A. G. Fowler, M. Mariantoni, J. M. Martinis, and A. N. Cleland, “Surface codes: Towards practical large-scale quantum computation,” Physical Review A, vol. 86, no. 3, Sep. 2012, issn: 1094-1622. doi: 10.1103/physreva.86.032324. (https://doi.org/10.1103/physreva.86.032324) [Online]. Available: http://dx.doi.org/10.1103/PhysRevA.86.032324. (http://dx.doi.org/10.1103/PhysRevA.86.032324)
[5] C. Gidney, “How to factor 2048 bit rsa integers with less than a million noisy qubits,” 2025. arXiv: 2505.15917 [quant-ph]. [Online]. Available: https://arxiv.org/abs/2505.15917.
[6] G. Scappucci et al., “The germanium quantum information route,” Nature Reviews Materials, vol. 6, no. 10, pp. 926–943, Dec. 2020, issn: 2058-8437. doi: 10.1038/s41578-020-00262-z. (https://doi.org/10.1038/s41578-020-00262-z) [Online]. Available: http://dx.doi.org/10.1038/s41578-020-00262-z.
[7] V. John et al., “A two-dimensional 10-qubit array in germanium with robust and localised qubit control,” 2025. arXiv: 2412.16044 [cond-mat.mes-hall]. (https://arxiv.org/abs/2412.16044) [Online]. Available: https: //arxiv.org/abs/2412.16044.
[8] N. W. Hendrickx et al., “Sweet-spot operation of a germanium hole spin qubit with highly anisotropic noise sensitivity,” Nature Materials, vol. 23, no. 7, pp. 920–927, May 2024, issn: 1476-4660. doi: 10.1038/s41563-024-01857-5. (https://doi.org/10.1038/s41563-024-01857-5) [Online]. Available: http://dx.doi.org/10.1038/s41563-024-01857-5. (http://dx.doi.org/10.1038/s41563-024-01857-5)
[9] C. X. Yu et al., “Optimising germanium hole spin qubits with a room-temperature magnet,” 2025. arXiv: 2507.03390 [quant-ph]. (https://arxiv.org/abs/2507.03390) [Online]. Available: https://arxiv.org/abs/2507. 03390. (https://arxiv.org/abs/2507.03390)
[10] G. Da Prato, Y. Yu, R. Bode, and S. Gr¨oblacher, “Step-by-step design guide of a cryogenic three-axis vector magnet,” Review of Scientific Instruments, vol. 96, no. 6, Jun. 2025, issn: 1089-7623. doi: 10.1063/5.0270187. (https://doi.org/10.1063/5.0270187) [Online]. Available: http://dx.doi.org/10.1063/5. 0270187. (http://dx.doi.org/10.1063/5.0270187)
[11] C. Adambukulam et al., “An ultra-stable 1.5 T permanent magnet assembly for qubit experiments at cryogenic temperatures,” Review of Scientific Instruments, vol. 92, no. 8, 2021.

[12] Proteox MX dilution refrigerator, https://nanoscience.oxinst.com/products/proteoxmx, Accessed: 31-10-2025.
[13] M. Ortner and L. G. C. Bandeira, “Magpylib: A free python package for magnetic field computation,” SoftwareX, vol. 11, p. 100 466, 2020.
[14] Michael-Ortner et al., Magpylib, version 5.2.1, Jun. 25, 2023. [Online]. Available: https : //magpylib.readthedocs.io/en/latest/.
[15] C.-A. Wang et al., “Operating semiconductor quantum processors with hopping spins,” Science, vol. 385, no. 6707, pp. 447–452, 2024. doi: 10.1126/science.ado5915. (https://doi.org/10.1126/science.ado5915) eprint: https: //www.science.org/doi/pdf/10.1126/science.ado5915. [Online]. Available: https: //www.science.org/doi/abs/10.1126/science.ado5915.
[16] Magnet-positioner-project, https : / / github . com / iDragos1234 / Magnet - Positioner -Project, (https://github.com/iDragos1234/Magnet-Positioner-Project) GitHub repository., 2025.

## A Maximum weight calculation of NEMA 17 stepper motors

Given that a single stepper motor has a maximum holding torque of τ = 0.55 Nm and a lead screw radius of r = 4 mm, it easily follows from the torque formula

τ = r × FE,

that the effort force is FE = 137.5 N. The efficiency of the lead screw is given by

η =

tan(α)
tan(α + β)

,

where α is the lead angle and β is the friction angle. Given that the lead screw has a pitch P = 2 mm and assuming the coefficient of friction between the rotating components is f = 0.3, we find α = tan⁻¹
(

P
2πr

) ≈ 4.550◦ and β = tan⁻¹

(f) ≈ 16.699◦
. Therefore the lead screw has an efficiency of η ≈ 20.4%.
Using this and the velocity ratio of the lead screw V R = 2πr/P = 4π, it follows that the mechanical advantage is MA = V R · η ≈ 2.57. Finally, the load force is given by

FL = FE · MA

resulting in FL = 353.6 N, or equivalently a weight of around 36 kg per motor.

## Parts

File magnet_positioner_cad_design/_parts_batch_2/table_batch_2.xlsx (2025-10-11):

Item number | Item | Part file (.stp) | Drawing file (.pdf) | Quantity | Material | Other specifications
#1 | Z-plate | z_plate.stp | z_plate.pdf | x1 | Aluminium alloy | Apply deburring on sharp edges and corners as needed
#2 | X-plate | x_plate.stp | x_plate.pdf | x1 | Aluminium alloy | Apply deburring on sharp edges and corners as needed

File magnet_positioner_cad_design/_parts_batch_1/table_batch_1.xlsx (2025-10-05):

Item number | Item | Part file (.stp) | Drawing file (.pdf) | Quantity | Material | Other specifications
#1 | Half ring | half_ring.stp | half_ring.pdf | x2 | Aluminium alloy | Apply deburring on sharp edges and corners as needed
#2 | Base plate | base_plate.stp | base_plate.pdf | x1 | Aluminium alloy | Apply deburring on sharp edges and corners as needed
#3 | Z-rail bracket | z_rail_bracket.stp | z_rail_bracket.pdf | x2 | Stainless steel | Apply deburring on sharp edges and corners as needed
#4 | Z-translator bracket | z_translator_bracket.stp | z_translator_bracket.pdf | x2 | Stainless steel | Apply deburring on sharp edges and corners as needed
#5 | Z-plate bracket | z_plate_bracket.stp | z_plate_bracket.pdf | x2 | Stainless steel | Apply deburring on sharp edges and corners as needed
#6 | Profile bars | profile_bar.stp | N/A | x4 | Aluminium alloy | Size 40x40. Length 850 mm. Threading for M8 screws

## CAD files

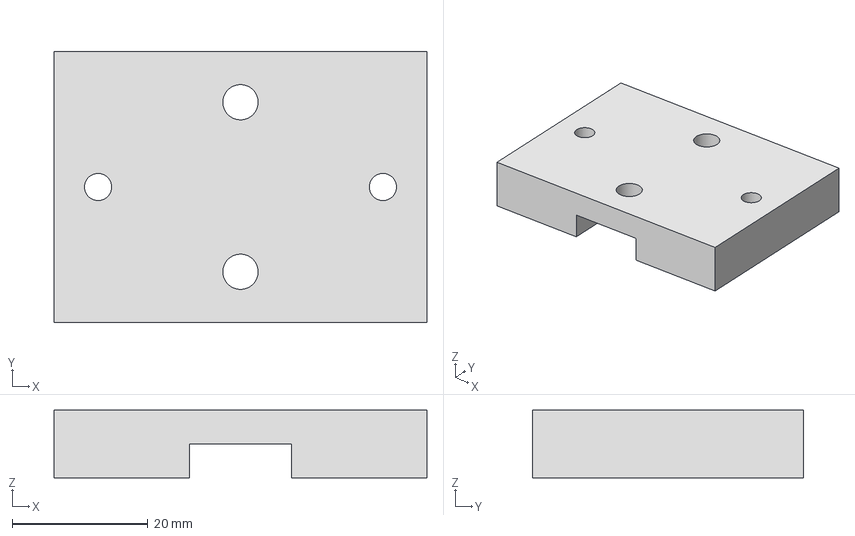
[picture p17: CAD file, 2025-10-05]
magnet_positioner_cad_design/_parts_batch_1/z_translator_bracket.stp
55.0 x 40.0 x 10.0 mm

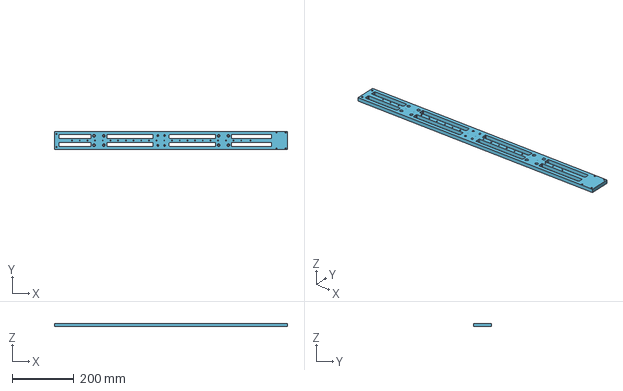
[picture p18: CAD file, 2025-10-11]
magnet_positioner_cad_design/_parts_batch_2/x_plate.stp
757.5 x 60.0 x 10.0 mm

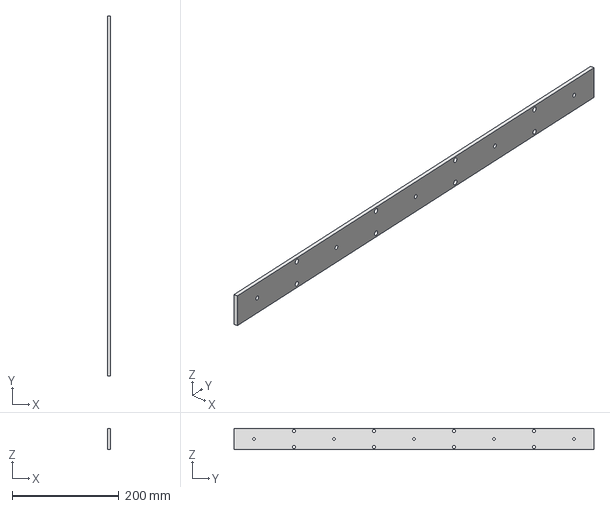
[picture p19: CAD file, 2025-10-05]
magnet_positioner_cad_design/_parts_batch_1/z_rail_bracket.stp
5.00 x 675.0 x 40.0 mm

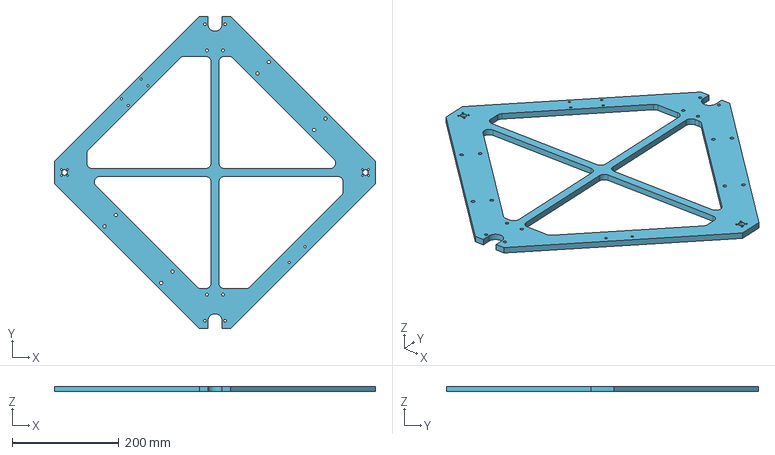
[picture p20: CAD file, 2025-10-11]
magnet_positioner_cad_design/_parts_batch_2/z_plate.stp
601.0 x 585.0 x 10.0 mm

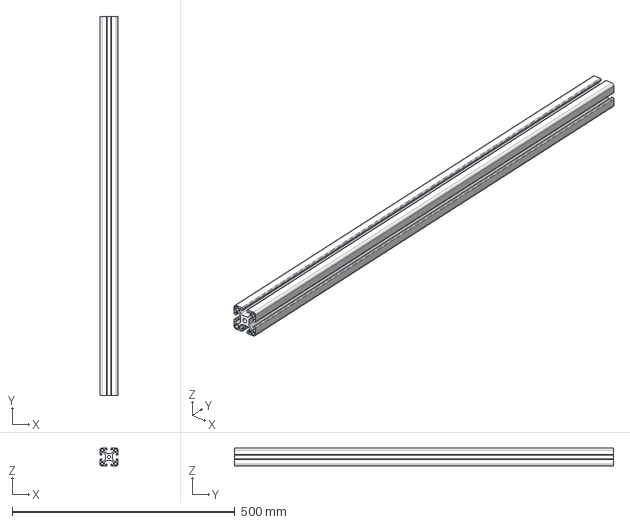
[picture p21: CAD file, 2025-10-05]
magnet_positioner_cad_design/_parts_batch_1/profile_bar.stp
40.0 x 850.0 x 40.0 mm

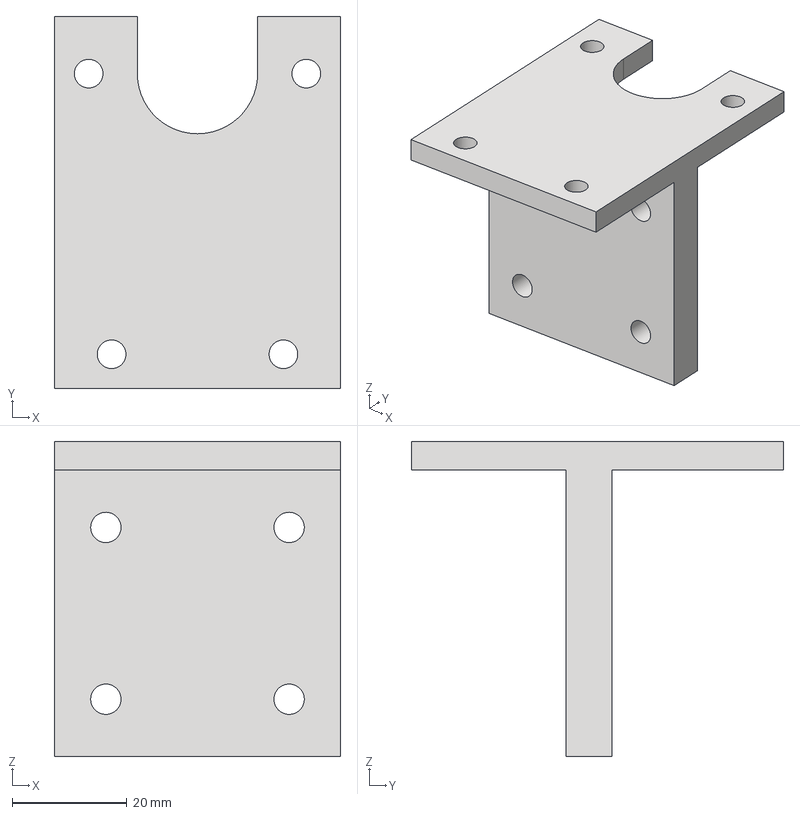
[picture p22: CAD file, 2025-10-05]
magnet_positioner_cad_design/_parts_batch_1/z_plate_bracket.stp
50.0 x 65.0 x 55.0 mm

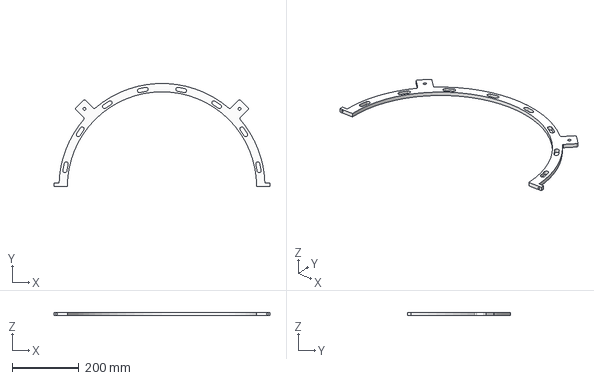
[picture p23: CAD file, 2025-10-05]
magnet_positioner_cad_design/_parts_batch_1/half_ring.stp
645.0 x 307.2 x 10.0 mm

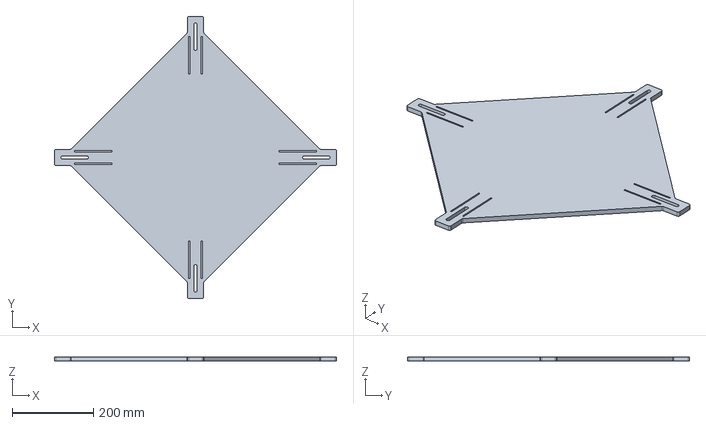
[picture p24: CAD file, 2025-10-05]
magnet_positioner_cad_design/_parts_batch_1/base_plate.stp
695.0 x 695.0 x 10.0 mm

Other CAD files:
magnet_positioner_cad_design/drawings/z_plate.dwg
magnet_positioner_cad_design/drawings/x_plate.dwg
magnet_positioner_cad_design/gantry_frame/half_ring.dwg
magnet_positioner_cad_design/drawings/half_ring.dwg
magnet_positioner_cad_design/gantry_frame/Rail_bracket.dwg
magnet_positioner_cad_design/gantry_frame/base_plate.dwg
magnet_positioner_cad_design/drawings/Rail_bracket.dwg
magnet_positioner_cad_design/drawings/base_plate.dwg
magnet_positioner_cad_design/gantry_frame/Leadscrew Bearing Bracket.dwg
magnet_positioner_cad_design/drawings/Leadscrew Bearing Bracket.dwg
magnet_positioner_cad_design/gantry_frame/base_plate.ipt
magnet_positioner_cad_design/gantry_frame/full_ring.iam
magnet_positioner_cad_design/gantry_frame/gantry_frame.iam
magnet_positioner_cad_design/gantry_frame/half_ring.ipt
magnet_positioner_cad_design/gantry_frame/square_bar.ipt
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

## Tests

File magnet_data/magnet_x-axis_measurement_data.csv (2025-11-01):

 | Magnet-sensor distance [cm] | Bx[mT] | By[mT] | Bz[mT] | Bx[LSB] | By[LSB] | Bz[LSB] | Temperature[C] | Mode[MCM=0,ULOW_POWER=1,LOW_POWER=2,FAST=3]
0 | 0 | -54.95 | -277.63 | 24.95 | -1621 | -8190 | 736 | 20.26 | 2
1 | 0 | -55.05 | -277.63 | 24.95 | -1624 | -8190 | 736 | 20.33 | 2
2 | 0 | -54.92 | -277.63 | 24.92 | -1620 | -8190 | 735 | 20.39 | 2
3 | 0 | -54.88 | -277.63 | 24.88 | -1619 | -8190 | 734 | 20.39 | 2
4 | 0 | -55.08 | -277.63 | 24.92 | -1625 | -8190 | 735 | 20.13 | 2
5 | 0 | -54.98 | -277.63 | 24.88 | -1622 | -8190 | 734 | 20.39 | 2
6 | 0 | -55.02 | -277.63 | 24.81 | -1623 | -8190 | 732 | 20.13 | 2
7 | 0 | -54.95 | -277.63 | 24.88 | -1621 | -8190 | 734 | 20.33 | 2
8 | 0 | -55.08 | -277.63 | 24.88 | -1625 | -8190 | 734 | 20.39 | 2
9 | 0 | -55.02 | -277.63 | 24.85 | -1623 | -8190 | 733 | 20.39 | 2
10 | 0 | -54.92 | -277.63 | 25.02 | -1620 | -8190 | 738 | 20.33 | 2
11 | 0 | -54.98 | -277.63 | 24.85 | -1622 | -8190 | 733 | 20.53 | 2
12 | 0 | -54.95 | -277.63 | 24.88 | -1621 | -8190 | 734 | 20.26 | 2
13 | 0 | -54.81 | -277.63 | 24.95 | -1617 | -8190 | 736 | 20.39 | 2
14 | 0 | -55.02 | -277.63 | 24.85 | -1623 | -8190 | 733 | 20.53 | 2
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

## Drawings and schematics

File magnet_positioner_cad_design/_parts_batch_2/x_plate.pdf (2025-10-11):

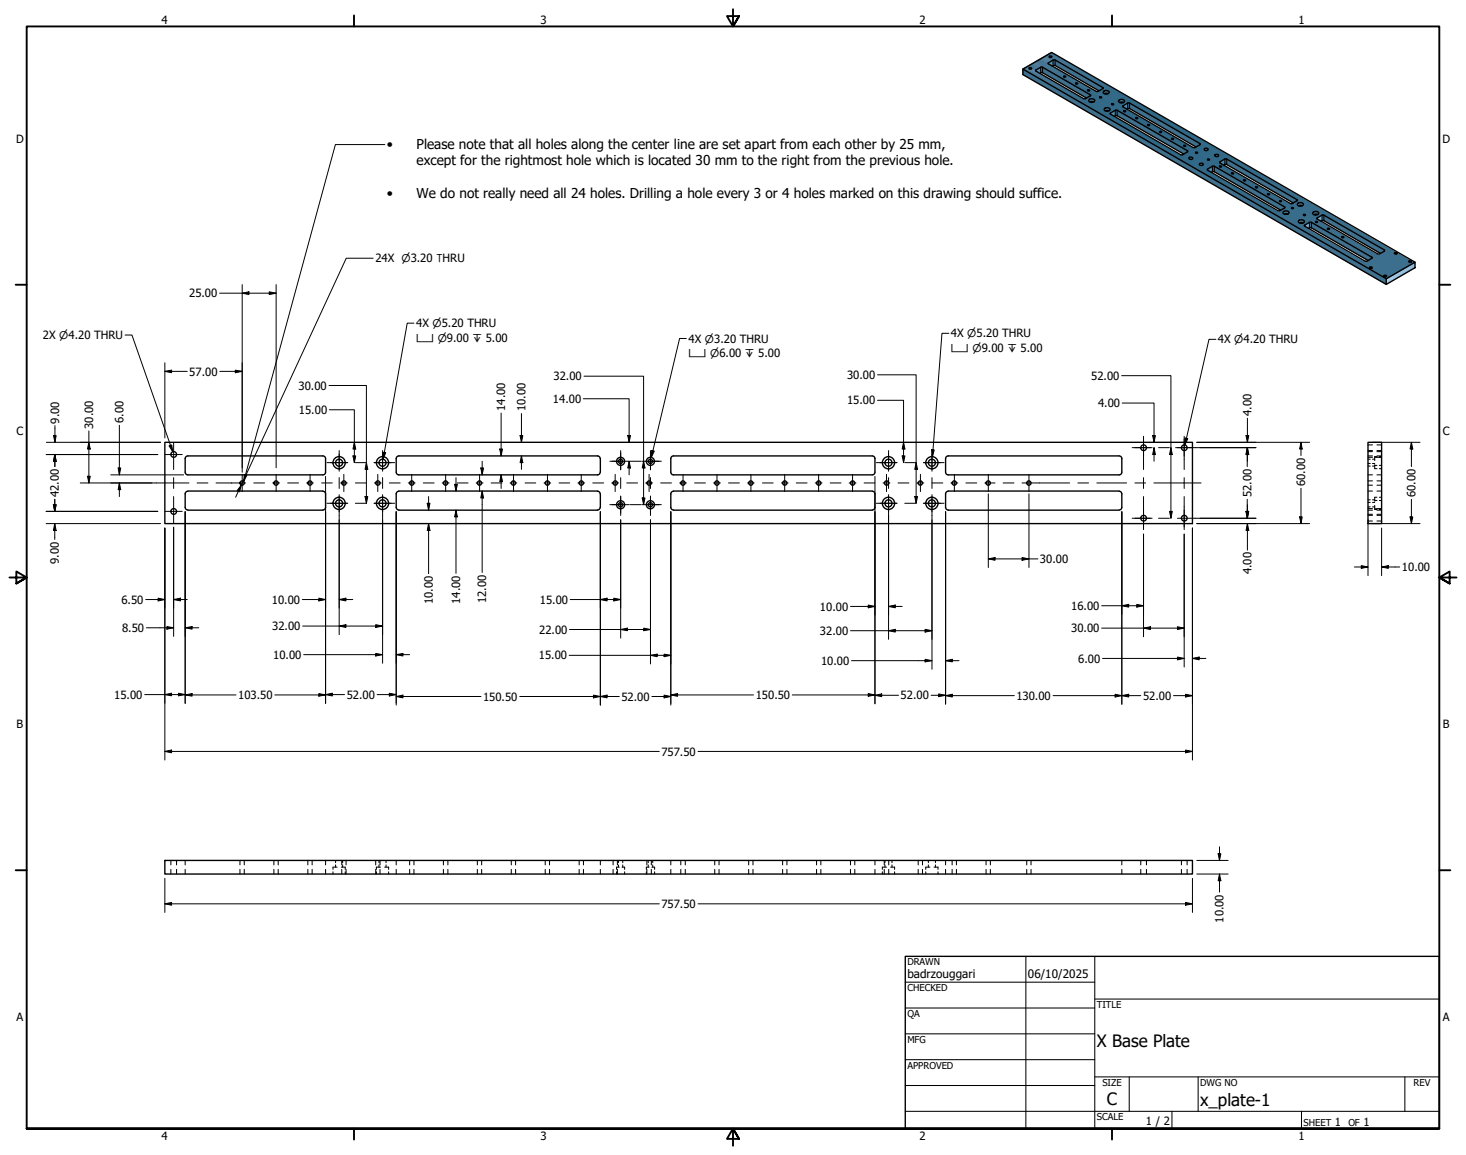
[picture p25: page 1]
X Base Plate; 2X ⌀4.20 THRU; 4X ⌀5.20 THRU ⌴ ⌀9.00 ↧ 5.00; 4X ⌀3.20 THRU ⌴ ⌀6.00 ↧ 5.00; 4X ⌀4.20 THRU

• Please note that all holes along the center line are set apart from each other by 25 mm,
except for the rightmost hole which is located 30 mm to the right from the previous hole.

• We do not really need all 24 holes. Drilling a hole every 3 or 4 holes marked on this drawing should suffice.

DRAWN badrzouggari | 06/10/2025

CHECKED

MFG

APPROVED

SIZE C | DWG NO x_plate-1 | REV

SCALE 1 / 2 | | SHEET 1 OF 1

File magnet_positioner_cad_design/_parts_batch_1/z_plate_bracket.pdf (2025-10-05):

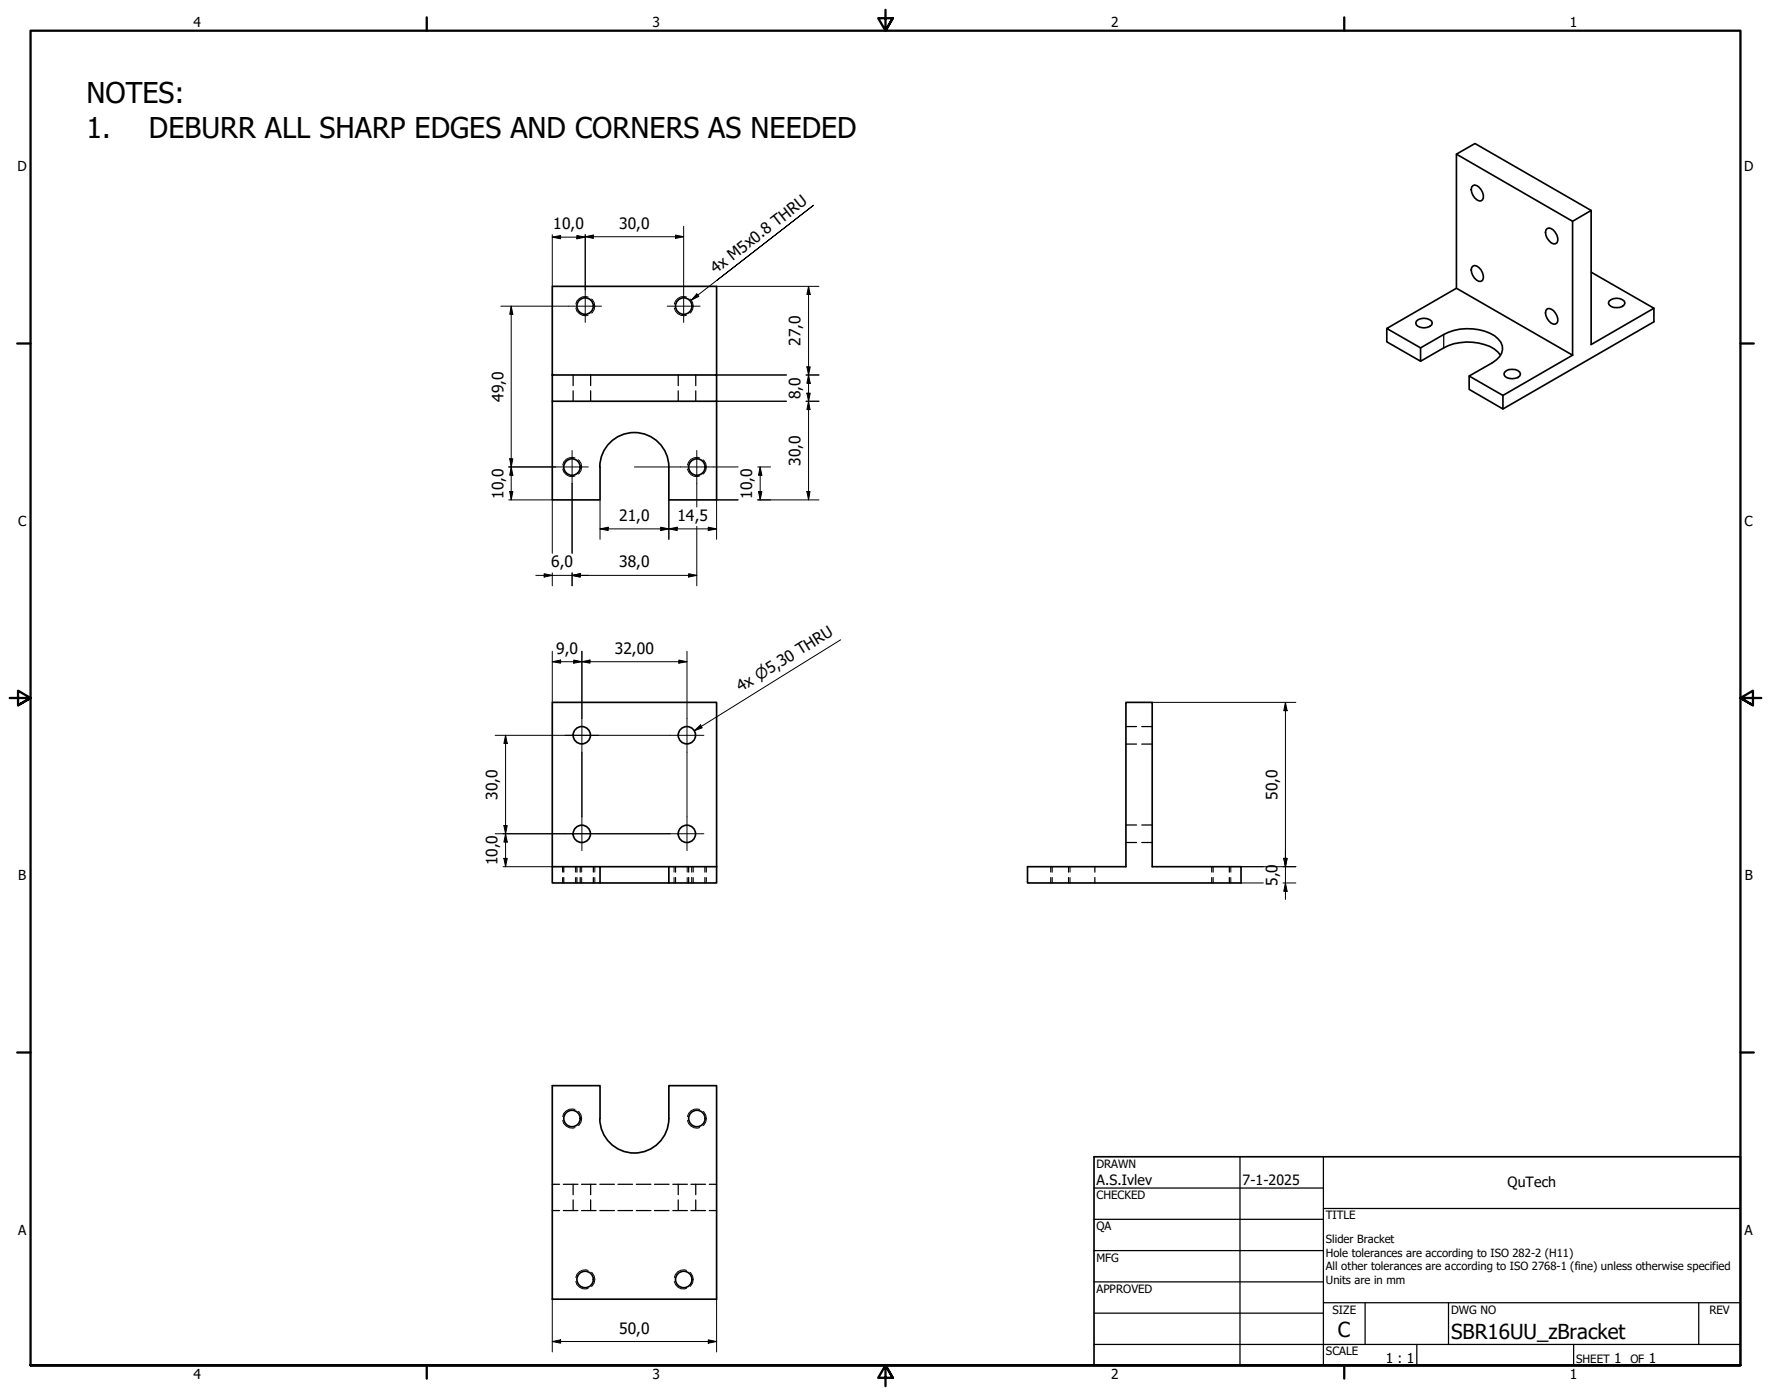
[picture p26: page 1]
4x ⌀5,30 THRU

NOTES:
1. DEBURR ALL SHARP EDGES AND CORNERS AS NEEDED

DRAWN A.S.Ivlev | 7-1-2025 | QuTech

CHECKED

Slider Bracket
Hole tolerances are according to ISO 282-2 (H11)
All other tolerances are according to ISO 2768-1 (fine) unless otherwise specified
Units are in mm

MFG

APPROVED

SIZE C | DWG NO SBR16UU_zBracket | REV

SCALE 1 : 1 | | SHEET 1 OF 1

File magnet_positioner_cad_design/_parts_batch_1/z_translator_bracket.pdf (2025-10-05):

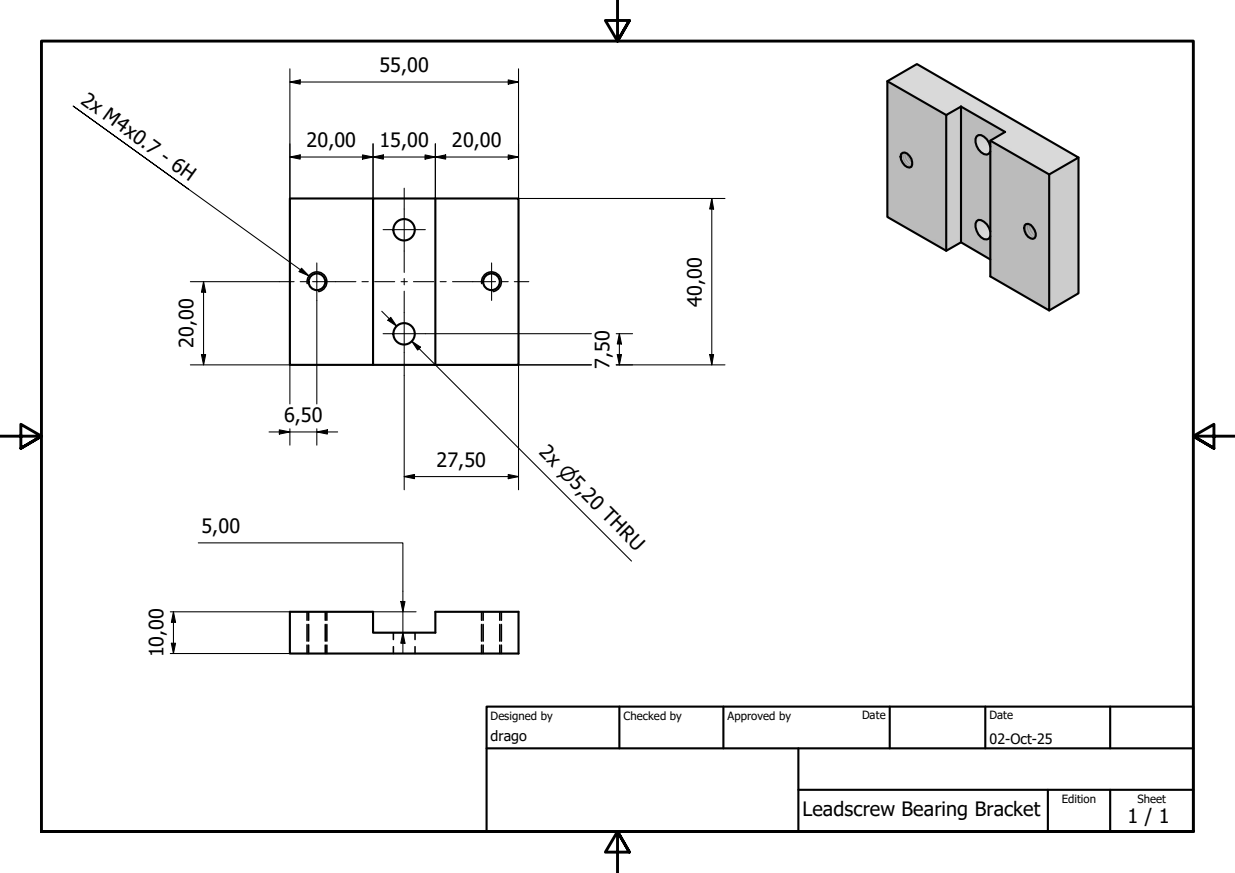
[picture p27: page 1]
Designed by; Checked by; Approved by; Date

Leadscrew Bearing Bracket

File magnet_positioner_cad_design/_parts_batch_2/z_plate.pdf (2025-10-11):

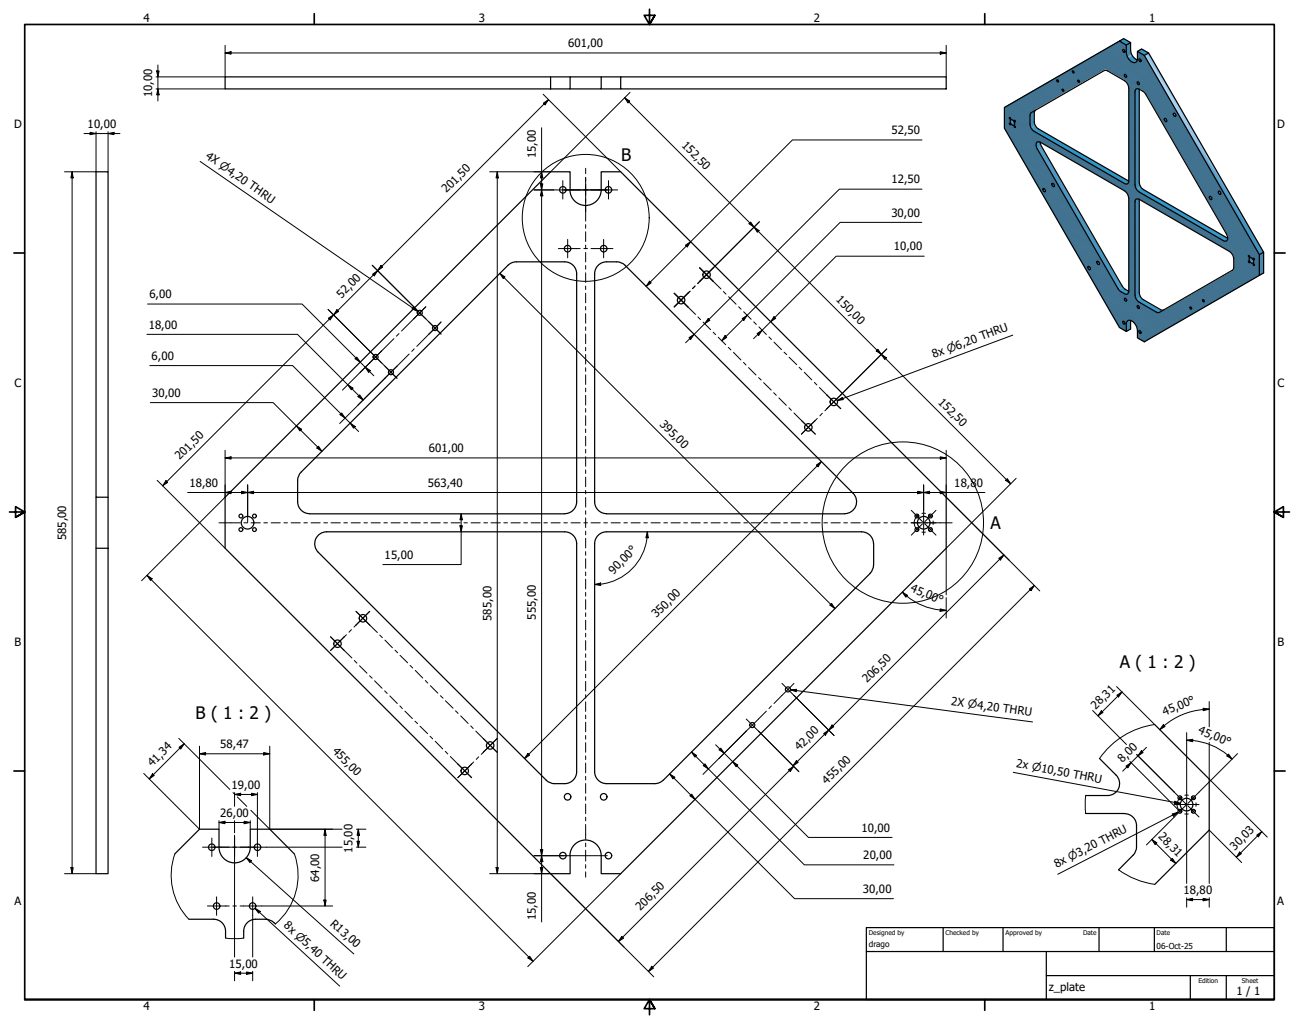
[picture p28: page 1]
,20 THRU; 8x ⌀5,40 THRU; 4X ⌀4,20 THRU

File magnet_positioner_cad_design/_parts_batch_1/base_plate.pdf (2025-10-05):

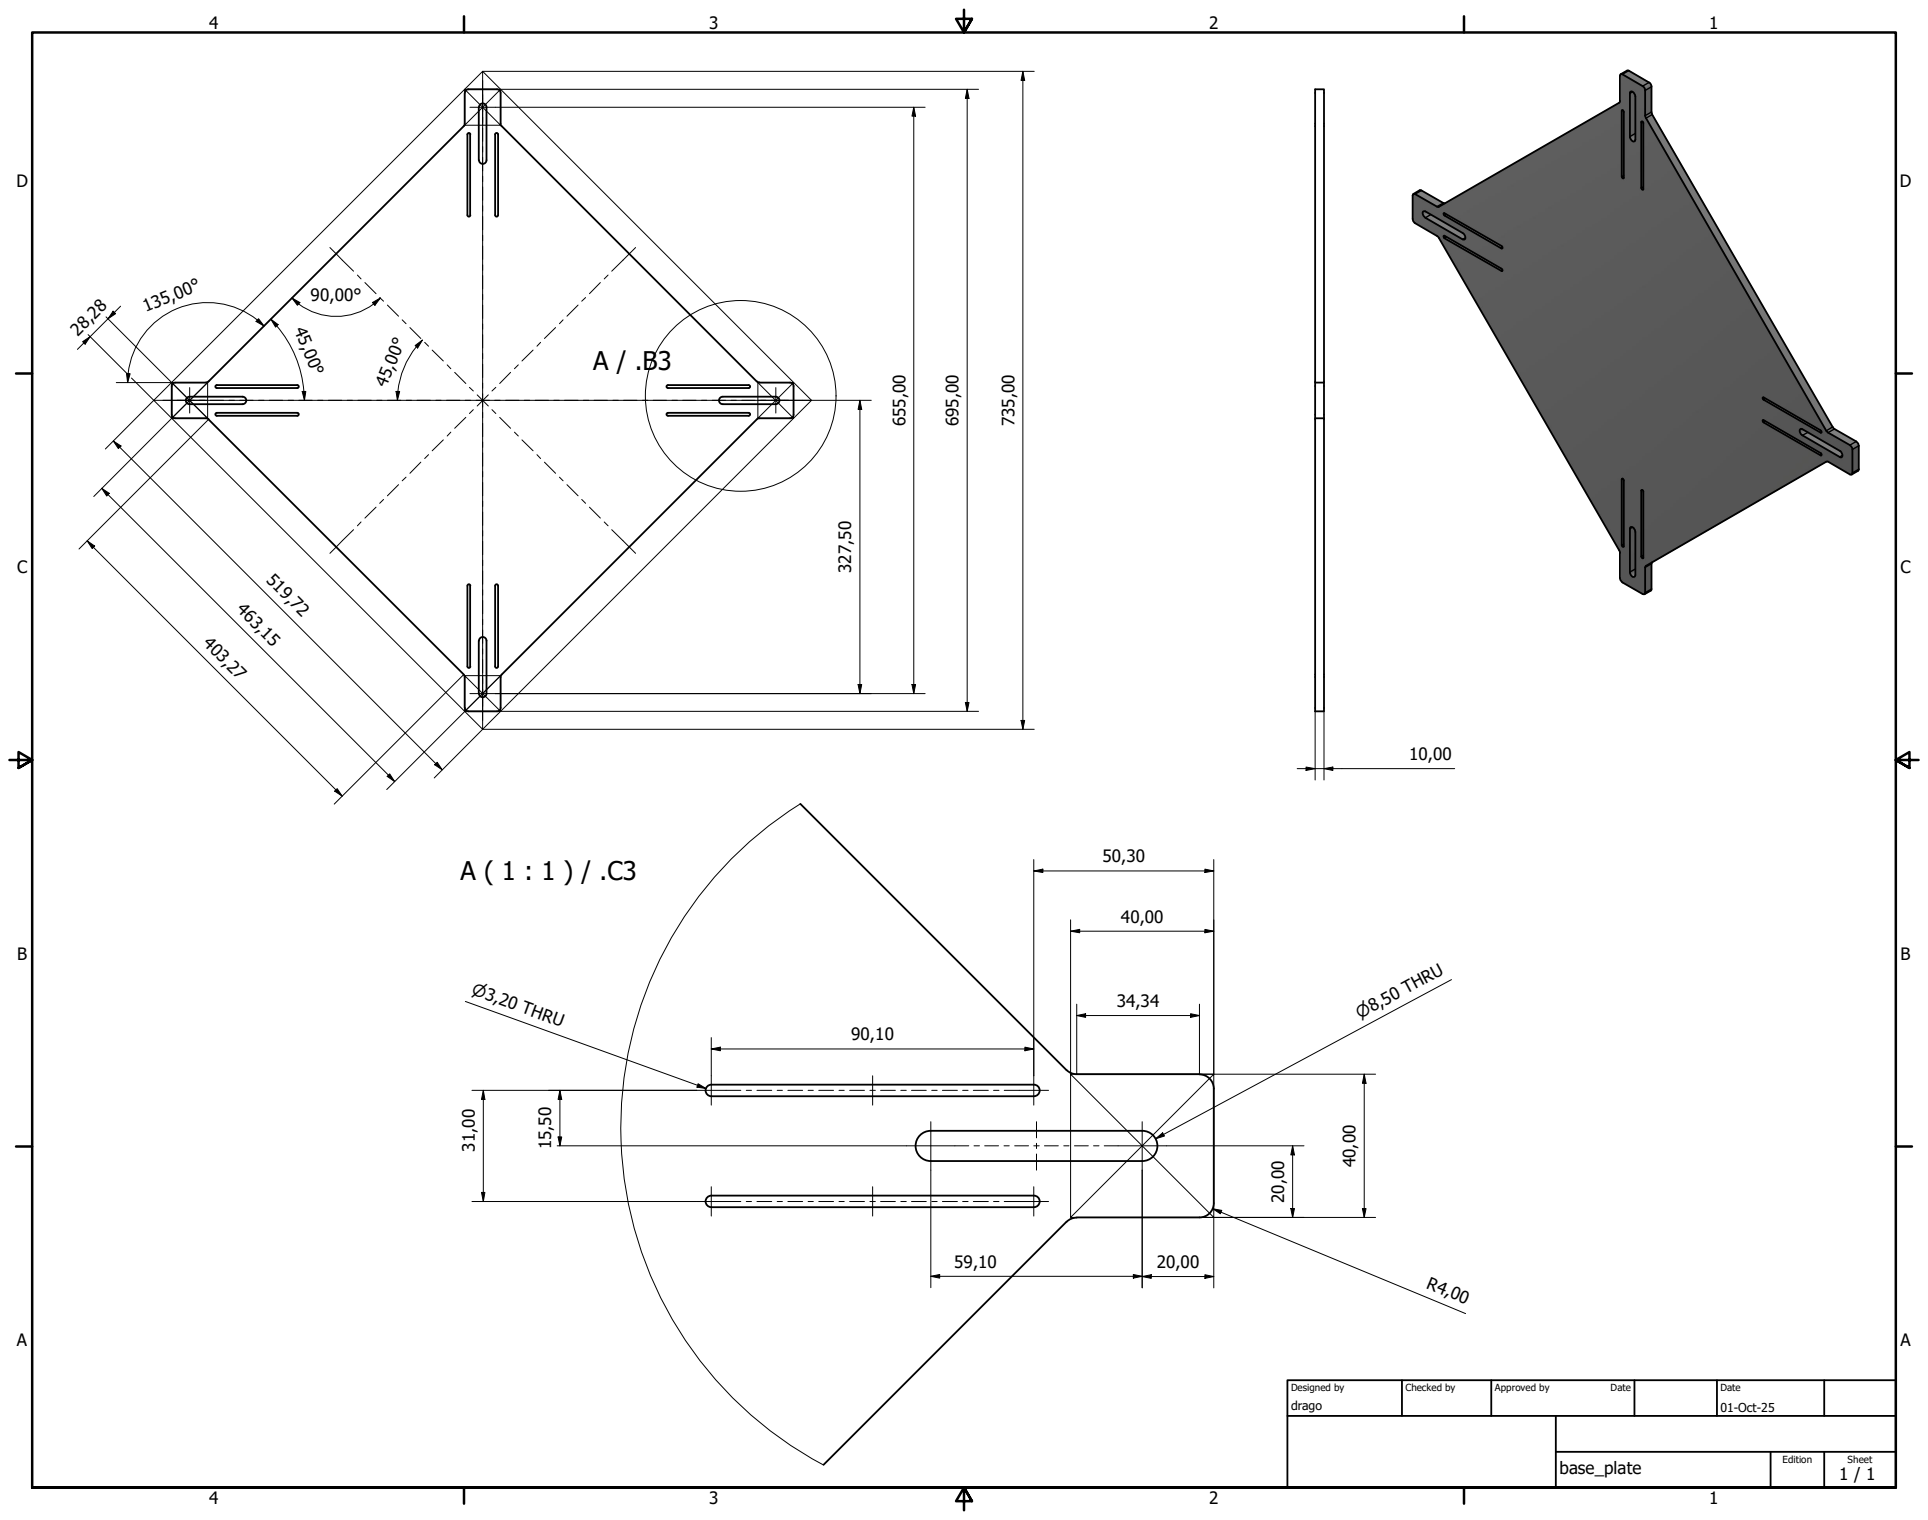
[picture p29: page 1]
Designed by; Checked by; Approved by; Date; ⌀8,50 THRU; ⌀3,20 THRU

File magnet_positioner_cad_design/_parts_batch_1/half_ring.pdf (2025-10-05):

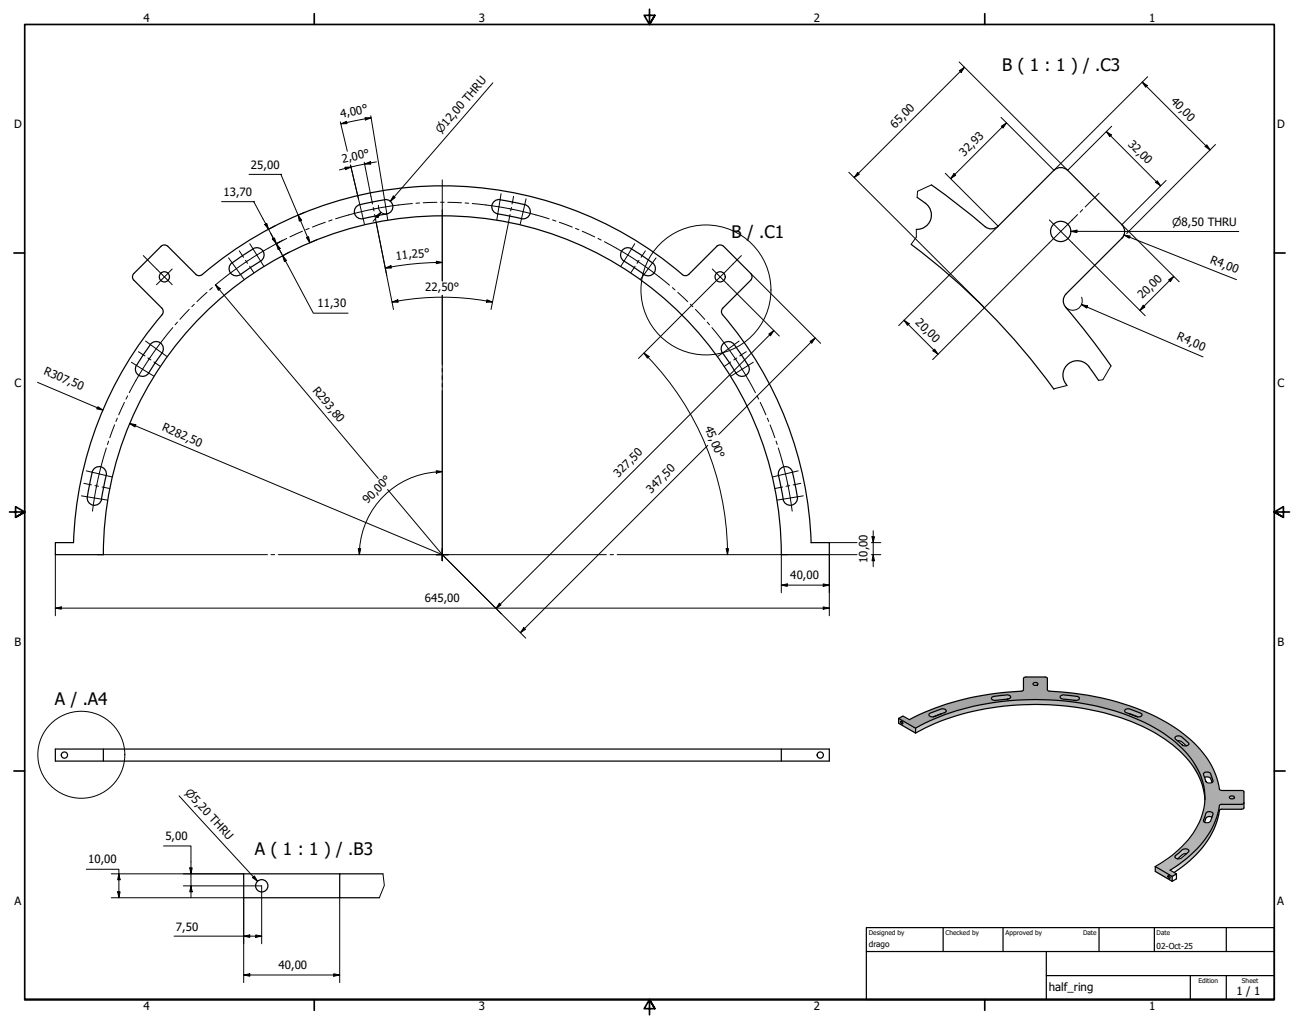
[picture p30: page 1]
Designed by; Checked by; Approved by; Date; ⌀5,20 THRU; ⌀8,50 THRU; ⌀12,00 THRU

half_ring | Edition | Sheet 1 / 1

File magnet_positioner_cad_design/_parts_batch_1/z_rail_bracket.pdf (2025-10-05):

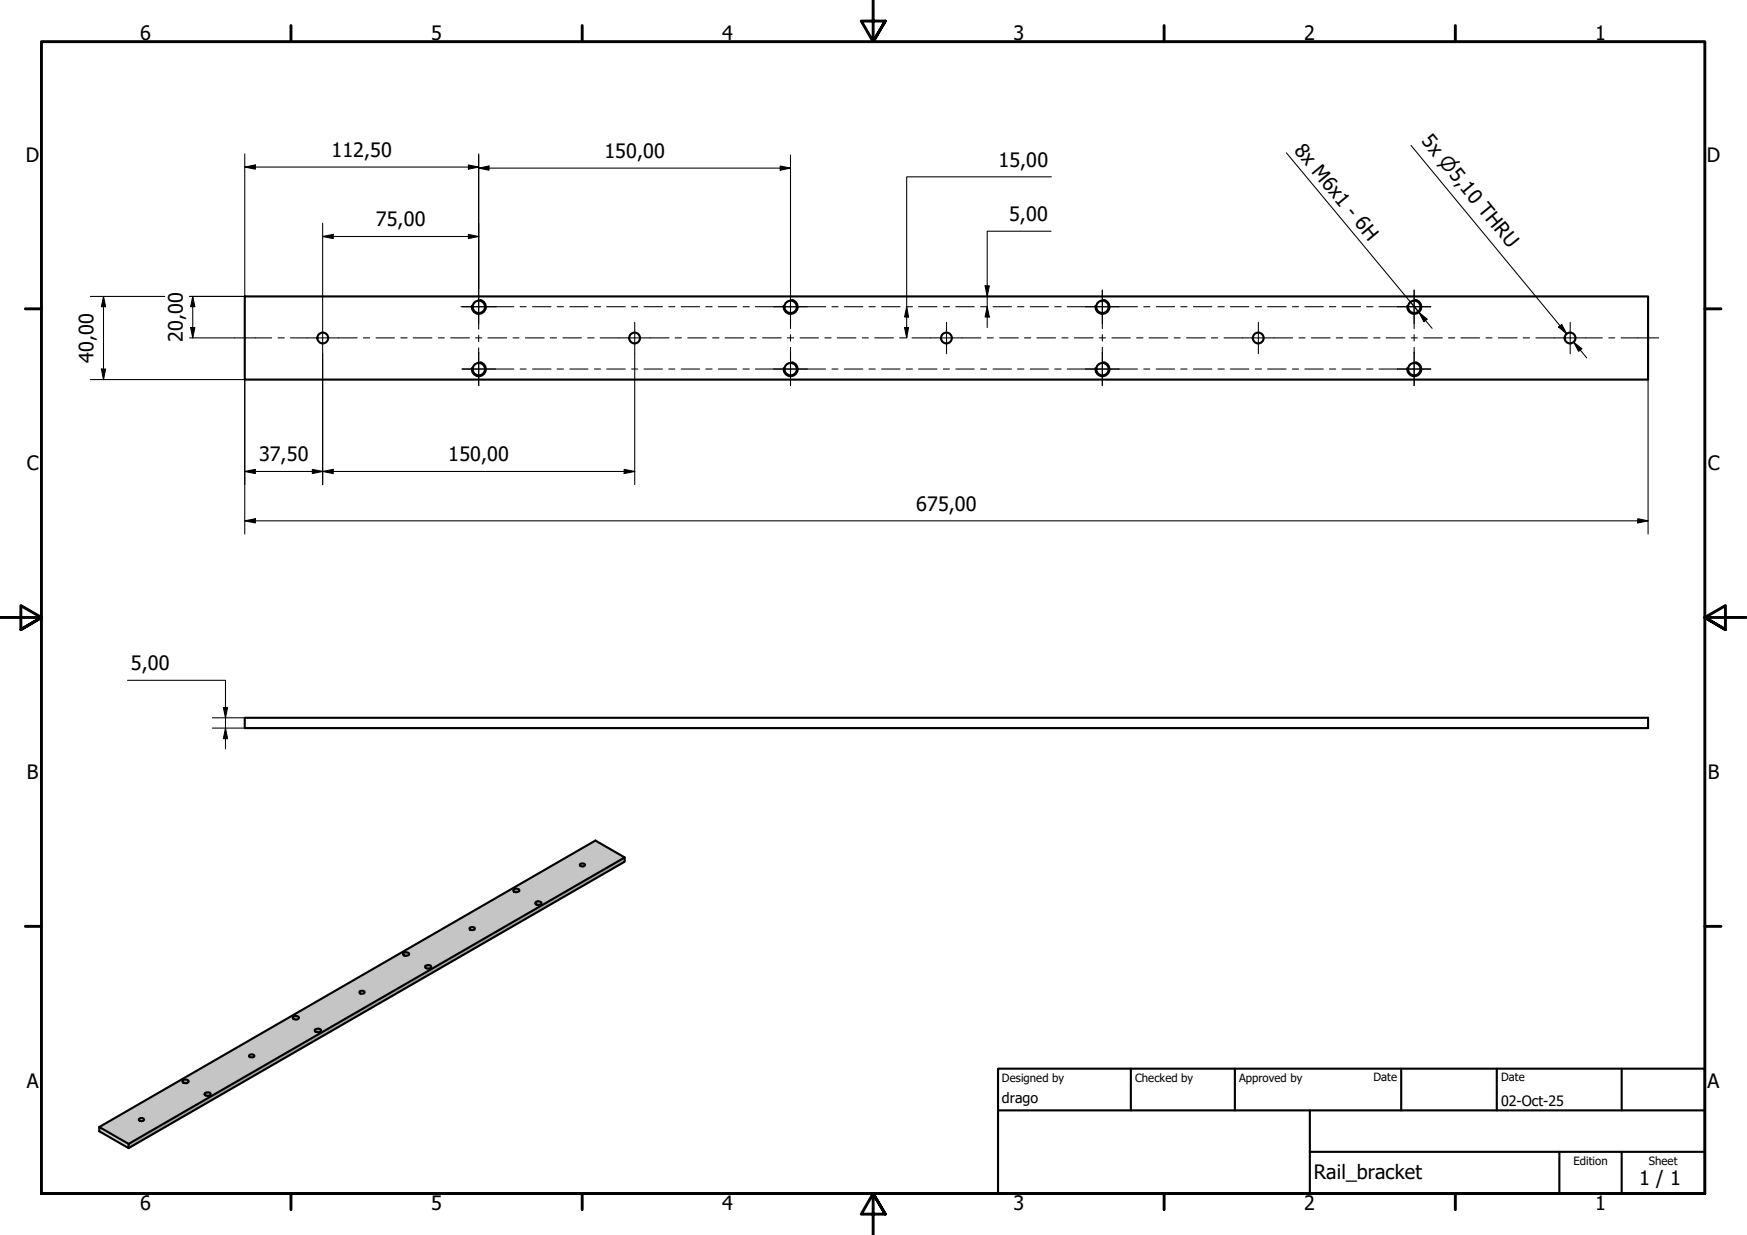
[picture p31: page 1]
Designed by; Checked by; Approved by; Date

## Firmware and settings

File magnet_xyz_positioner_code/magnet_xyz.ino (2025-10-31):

#include <EEPROM.h>
#include <AccelStepper.h>

// Define motor driver type (1 = Driver, uses STEP and DIR)
#define DRIVER 1

// Stepper motor definitions (STEP, DIR)
AccelStepper stepperX(DRIVER, 2, 5);  // X-axis
AccelStepper stepperY(DRIVER, 3, 6);  // Y-axis
AccelStepper stepperZ(DRIVER, 4, 7);  // Z-axis

// CNC Shield Enable Pin (shared for all motors)
const int enPin = 8; // ENABLE pin for all motors

// EEPROM Addresses
constexpr int EEPROM_ADDR[] = {0, 4, 8}; // x, y, z

// Stepper motor settings (individual for each axis)
constexpr int maxSpeedX = 100;   // X max speed (steps per second)
constexpr int accelerationX = 100; // X acceleration (steps per second²)

constexpr int maxSpeedY = 1000;   // Y max speed (steps per second)
constexpr int accelerationY = 2 * maxSpeedY; // Y acceleration (steps per second²)

constexpr int maxSpeedZ = 500;   // Z max speed (steps per second)
constexpr int accelerationZ = 500; // Z acceleration (steps per second²)

// Array of stepper motor pointers for easier handling
AccelStepper* steppers[] = {&stepperX, &stepperY, &stepperZ};

// Motor axis labels
constexpr char AXIS_LABELS[] = {'x', 'y', 'z'};

void setup() {
    Serial.begin(9600);

    pinMode(LED_BUILTIN, OUTPUT);
    pinMode(enPin, OUTPUT);

    // Disable motors at startup
    // Configure all steppers
    configureStepper(stepperX, maxSpeedX, accelerationX);
    configureStepper(stepperY, maxSpeedY, accelerationY);
    configureStepper(stepperZ, maxSpeedZ, accelerationZ);
    disableMotors();
}

// Configure stepper motor parameters
void configureStepper(AccelStepper &stepper, int maxSpeed, int acceleration) {
    stepper.setMaxSpeed(maxSpeed);
    stepper.setAcceleration(acceleration);
}

// Disable all motors (turns off holding torque)
void disableMotors() {
    digitalWrite(enPin, HIGH); // Disable all motors
}

// Enable motors before movement
void enableMotors() {
    digitalWrite(enPin, LOW); // Enable all motors
}

// Handle LED control commands
void handleLEDCommand(String command) {
    if (command == "L0") {
        digitalWrite(LED_BUILTIN, LOW);
        Serial.println("0");
    } else if (command == "L1") {
        digitalWrite(LED_BUILTIN, HIGH);
        Serial.println("1");
    } else if (command == "L?") {
        Serial.println(digitalRead(LED_BUILTIN) ? "1" : "0");
    } else {
        Serial.println("Invalid L command. Use L0, L1, or L?");
    }
}

  

// Handle movement and position queries for an axis
void handleAxisCommand(String command, int axisIndex) {
    if (command.endsWith("?")) {
        long stored_value;
        EEPROM.get(EEPROM_ADDR[axisIndex], stored_value);
        Serial.println(stored_value);
    } else {
        long value = command.substring(1).toInt();
        updatePosition(AXIS_LABELS[axisIndex], value);
    }
}

// Handle tare commands
void handleTareCommand(String command) {
    for (int i = 0; i < 3; i++) {
        if (command == "t" + String(AXIS_LABELS[i])) {
            EEPROM.put(EEPROM_ADDR[i], 0L);
            Serial.println(command);
            return;
        }
    }
    Serial.println("Invalid tare command: " + command);
}

// Move motor and update EEPROM
void updatePosition(char axis, long new_position) {
    int axisIndex = getAxisIndex(axis);
    if (axisIndex == -1) {
        Serial.println("Invalid axis");
        return;
    }

    long current_position;
    EEPROM.get(EEPROM_ADDR[axisIndex], current_position);

    if (current_position != new_position) { // Only move if position changes
        stepMotor(*steppers[axisIndex], new_position - current_position);
        EEPROM.put(EEPROM_ADDR[axisIndex], new_position);
    }
    Serial.println(axis);
}

// Step motor with acceleration
void stepMotor(AccelStepper &stepper, long steps) {
   // Enable motors before movement
    enableMotors();

    long targetPosition = stepper.currentPosition() + steps;
    stepper.moveTo(targetPosition);

    while (stepper.distanceToGo() != 0) {
        stepper.run();
    }
    disableMotors();
}

// Get the index of the axis ('x', 'y', 'z') for use in arrays
int getAxisIndex(char axis) {
    for (int i = 0; i < 3; i++) {
        if (AXIS_LABELS[i] == axis) return i;
    }
    return -1; // Invalid axis
}

void loop() {
    if (Serial.available()) {
        String command = Serial.readStringUntil('\n');
        command.trim();

        char cmdType = command.charAt(0);

        // LED Commands
        if (cmdType == 'L') {
            handleLEDCommand(command);
            return;
        }

        // Axis Movement Commands
        int axisIndex = getAxisIndex(cmdType);
        if (axisIndex != -1) {
            handleAxisCommand(command, axisIndex);
            return;
        }

        // Tare Commands
        if (cmdType == 't') {
            handleTareCommand(command);
            return;
        }


        Serial.println("Invalid command " + command);
    }
}

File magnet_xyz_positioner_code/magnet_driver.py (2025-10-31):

"""
Author: b-vanstraaten
Date: 20/02/2025
"""
from http.client import responses

import serial
from time import sleep
import serial.tools.list_ports
from qcodes import Instrument
from qcodes import validators as vals
from functools import partial

def convert_to_steps(x, mm_per_step, sign = 1):
    return int(x / mm_per_step) * sign

def convert_to_mm(x, mm_per_step, sign = 1):
    return float(x) * mm_per_step * sign



x_deg_per_step = 0.9
y_deg_per_step = 0.9
z_deg_per_step = 1.8

x_mm_per_turn = 2.0
y_mm_per_turn = 2.0
z_mm_per_turn = 2.0

x_mm_per_step = x_deg_per_step * x_mm_per_turn / 360
y_mm_per_step = y_deg_per_step * y_mm_per_turn / 360
z_mm_per_step = z_deg_per_step * z_mm_per_turn / 360

set_parsers = {
    'x': partial(convert_to_steps, mm_per_step=x_mm_per_step, sign = -1),
    'y': partial(convert_to_steps, mm_per_step=y_mm_per_step, sign = -1),
    'z': partial(convert_to_steps, mm_per_step=z_mm_per_step, sign = -1)
}

get_parsers = {
    'x': partial(convert_to_mm, mm_per_step=x_mm_per_step, sign = -1),
    'y': partial(convert_to_mm, mm_per_step=y_mm_per_step, sign = -1),
    'z': partial(convert_to_mm, mm_per_step=z_mm_per_step, sign = -1)
}

safety_distance = 5
bounds = {
    'x': (-255, 255),
    'y': (-60, 60),
    'z': (0, 555-safety_distance)
}

def list_serial_ports():
    """
    Lists available serial ports.
    Returns:
        list: A list of available serial ports.
    """
    ports = serial.tools.list_ports.comports()
    available_ports = []

    for port, desc, hwid in ports:
        available_ports.append(port)
        print(f"Port: {port} | Description: {desc} | HWID: {hwid}")

    if not available_ports:
        print("No serial ports found.")
    return available_ports


class ArduinoSerial(Instrument):
    """
    QCoDeS Instrument Driver for an Arduino over Serial Communication.
    """

    def __init__(self, name: str, port: str, baudrate: int = 9600, timeout: float = 1, **kwargs):
        """
        Initialise the Arduino serial driver.

        Args:
            name (str): Name of the instrument instance.
            port (str): Serial port for communication.
            baudrate (int): Baud rate for serial communication.
            timeout (float): Timeout for serial reads.
        """
        super().__init__(name, **kwargs)

        if port is None:
            list_serial_ports()
            raise ValueError("No port specified. Use list_serial_ports() to find available ports.")

        self.port = port
        self.baudrate = baudrate
        self.timeout = timeout

        # Establish connection
        self.connection = serial.Serial(port=self.port, baudrate=self.baudrate, timeout=self.timeout)
        sleep(2)  # Allow time for connection to establish
        print("Arduino initialised.")
        print(f"Connected to {self.port} at {self.baudrate} baud.")

        # Add LED control parameter
        self.add_parameter(
            name="LED",
            label="LED",
            get_cmd="L?",  # Query LED state
            set_cmd="L{}",  # Set LED state
            get_parser=int,
        )

        directions  = ["x", "y", "z"]
        current_position = {}

        for direction in directions:
            self.add_parameter(
                name = f'{direction}_step',
                label= f'{direction}_step',
                get_cmd=f"{direction}?",
                set_cmd=f"{direction}{{}}",
                get_parser=int,
            )

            set_parser = set_parsers[direction]
            get_parser = get_parsers[direction]

            self.add_parameter(
                name = f'{direction}',
                label= f'{direction}',
                get_cmd=f"{direction}?",
                set_cmd=f"{direction}{{}}",
                get_parser=get_parser,
                set_parser=set_parser,
                vals=vals.Numbers(*bounds[direction])
            )

        print('Current position:', self.position())

    def tare(self, coordinates = 'xyz'):
        for coordinate in coordinates:
            assert coordinate.lower() in ['x', 'y', 'z'], 'Invalid coordinate'
            self.ask(f't{coordinate.lower()}')


    def position(self, position = None):
        """
        Get the current position of the magnet.

        Returns:
            dict: The current position of the magnet.
        """
        position = {}
        for direction in ["x", "y", "z"]:
            position[direction] = getattr(self, direction).get()
        return position

    def ask(self, command: str):
        """
        Send a command to the Arduino and return the response.

        Args:
            command (str): The command string to send.

        Returns:
            str: The response from the Arduino.
        """
        return self.write(command)


    def write(self, command: str):
        """
        Send a command to the Arduino.

        Args:
            command (str): The command string to send.
        """
        if not self.connection.is_open:
            raise ConnectionError("Serial connection is not open.")

        self.connection.write(command.encode())

        message = ''
        while message == '':
            message = self.connection.readline().decode().strip()
            sleep(1e-2)
        return message

    def close(self):
        """
        Closes the serial connection.
        """
        if self.connection.is_open:
            self.connection.close()
            print(f"Connection to {self.port} closed.")

    def __del__(self):
        """Ensures proper cleanup on deletion."""
        self.close()


if __name__ == '__main__':
    menno = ArduinoSerial("arduino", "COM10")

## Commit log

2025-09-28 Model XY assembly
    [5X8_COUPLER.ipt, 608RS.ipt, KP08.iam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]
2025-09-30 Set profile height
    [5X8_COUPLER.ipt, 608RS.ipt, KP08.iam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]
2025-10-01 Re-sketch base plate
    [Stepper Motor Nema 17.ipt, Stepper Motor Nema 17_.ipt, base_plate - Copy.0035.ipt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]
2025-10-01 Re-sketch z-plate
    [base_plate - Copy.0035.ipt, base_plate - Copy.ipt, base_plate.0037.ipt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]
2025-10-05 Cut z-plate
    [Leadscrew Bearing Bracket.0002.ipt, Leadscrew Bearing Bracket.0003.dwg, Leadscrew Bearing Bracket.dwg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]
2025-10-05 Modify x-plate
    [half_ring.ipt, x_plate.ipt, y_rail.ipt]
2025-10-06 Modify magnet holder
    [magnet.ipt, magnet_holder.ipt, x_rail.ipt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]
2025-10-07 Draw z-plate and x-plate
    [x_plate.dwg, z_plate.dwg, z_plate.ipt]
2025-10-07 Change distance between x-rails
    [x_plate.dwg, x_plate.ipt, z_assembly.iam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]
2025-10-11 Prepare 2nd batch of parts and drawings
    [base_plate.stp, half_ring.stp, magnet_holder.ipt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]
2025-10-23 Modify magnet assembly
    [Leadscrew Bearing Bracket.ipt, Rail_bracket.ipt, gantry_frame.iam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]
2025-10-30 Add magnet measurements data
    [0.csv, 1.csv, 10.csv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]
2025-10-31 Create visualize magnet data.py
2025-10-31 Move files
    [Leadscrew Bearing Bracket.dwg, Rail_bracket.dwg, base_plate.dwg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]
2025-10-31 Change folder structure
    [5X8_COUPLER.ipt, 608RS.ipt, KP08.iam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]
2025-11-01 Change code for magnet data plot
    [magnet_x-axis_measurement_data.csv]
2025-11-06 Rename CAD part files
    [base_plate.ipt, gantry_frame.iam, half_ring.ipt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]
2025-11-06 Zip full assembly STEP file
2025-11-06 Motor codes
